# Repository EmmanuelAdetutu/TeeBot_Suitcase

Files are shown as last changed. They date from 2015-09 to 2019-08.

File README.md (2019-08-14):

# TeeBot_Suitcase!!
The folding Suitcase 3D printer.

Super thanks to all 42 Backers from Kickstarter for making this project possible. They all made it posible to share this project with everyone!!.

<b>***Teebot Specifications... Printed objects gallery</b> [Availaible here](http://3dstuffs.nl/teebot/)

<b>***Guide Photos of assembled sample</b> [Availaible here](https://www.flickr.com/photos/31259217@N06/albums/72157655761866343)

<b>***Youtube Video and print videos...</b>[Availaible here](https://www.youtube.com/watch?v=e_J-Re-Gbfc)

<b>***folow me on instagram...  </b>[#teebot3d](https://www.instagram.com/teebot3d/)

...always work in progress...

Comments, suggestion, contributions, errors,  info....what have you?
send me an email <b>info@3dstuffs.nl</b>

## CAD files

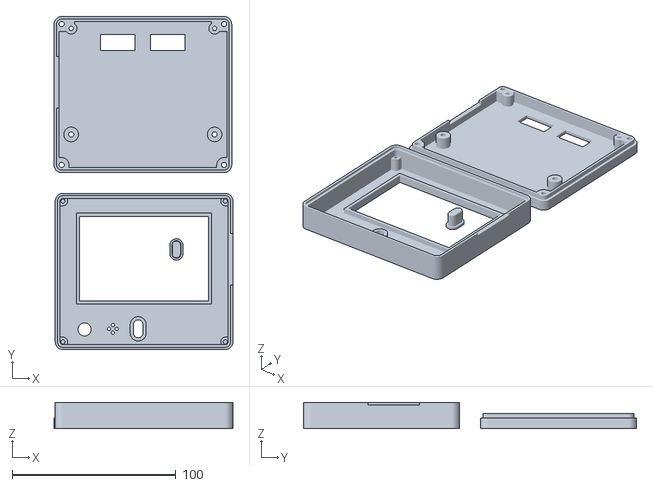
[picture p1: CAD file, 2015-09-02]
STL_Files/LCD_CASE_FULL_GRAPHIC.stl
109.3 x 203.5 x 16.1

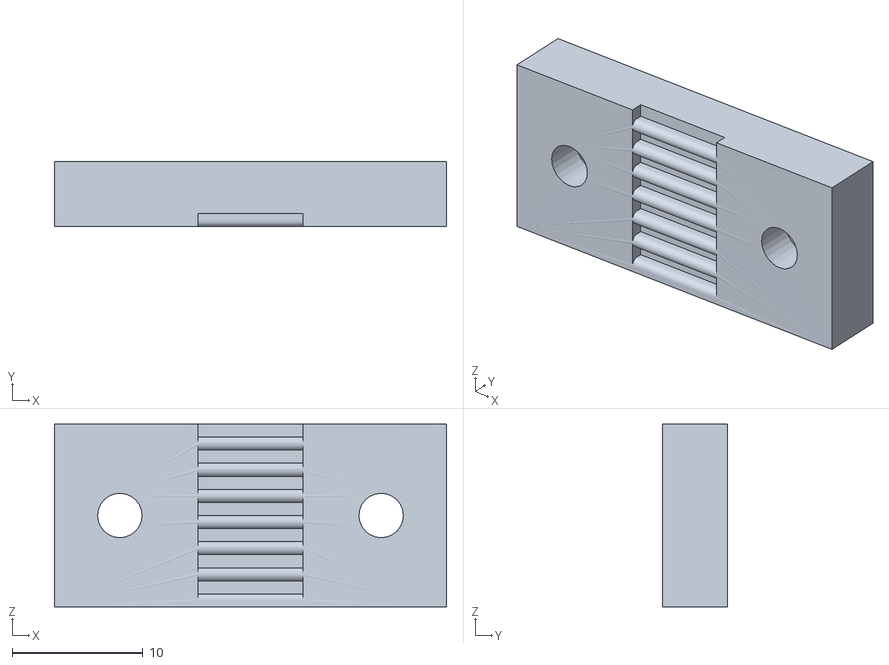
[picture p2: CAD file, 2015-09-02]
STL_Files/Y_Belt_Holder.stl
30.0 x 5.00 x 14.0

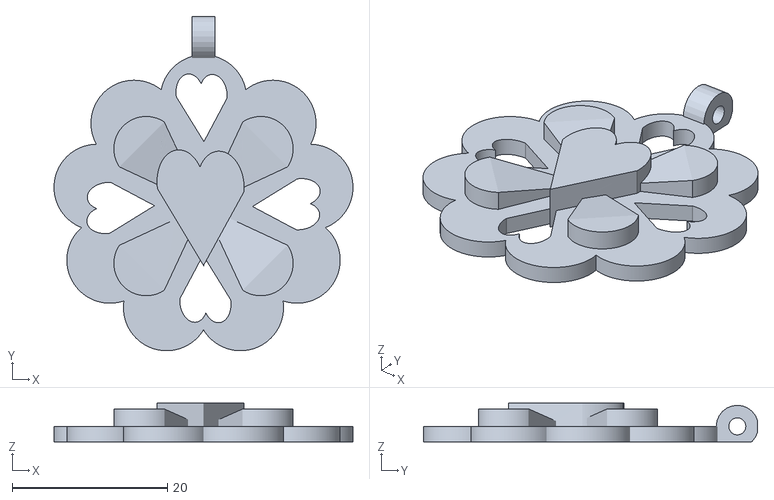
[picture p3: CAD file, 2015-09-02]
Test_STL_G_Code_Files/Test_Pendant.stl
38.6 x 43.1 x 5.00

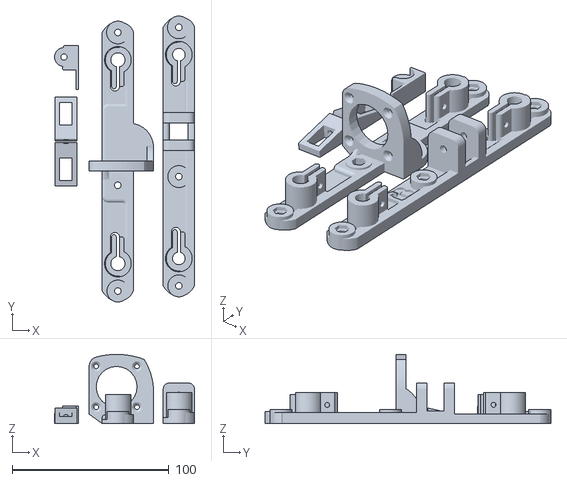
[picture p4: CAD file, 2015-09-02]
STL_Files/Y_Axis.stl
89.3 x 182.5 x 44.2

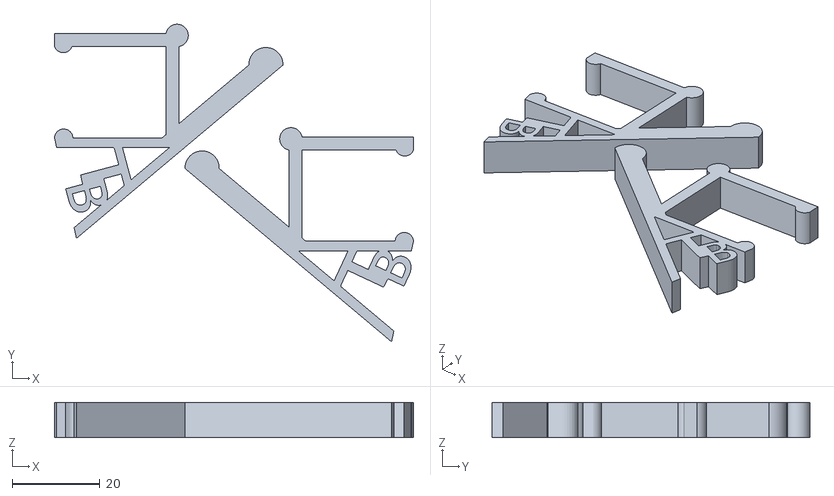
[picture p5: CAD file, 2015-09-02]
STL_Files/LCD_SUPPORT.stl
81.8 x 72.3 x 8.00

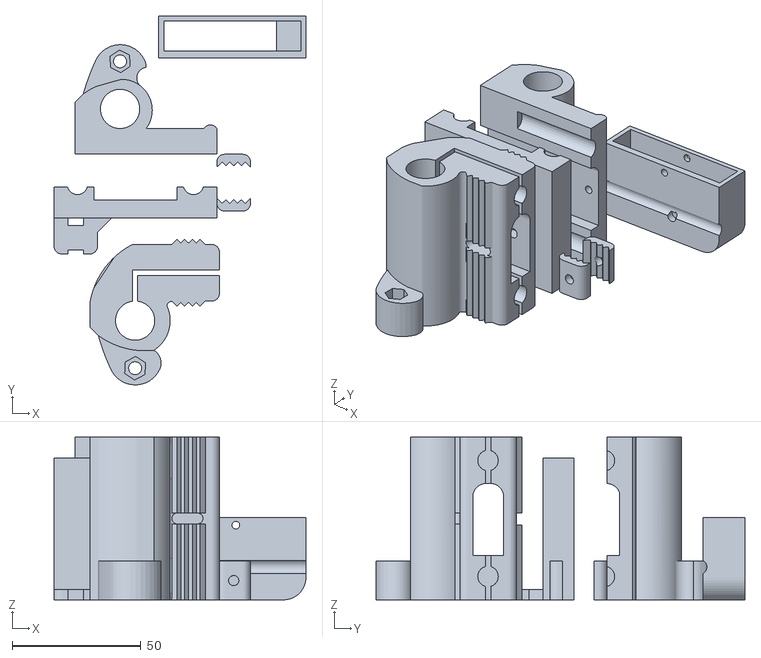
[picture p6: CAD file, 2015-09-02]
STL_Files/X_AXIS.stl
97.8 x 143.2 x 63.2

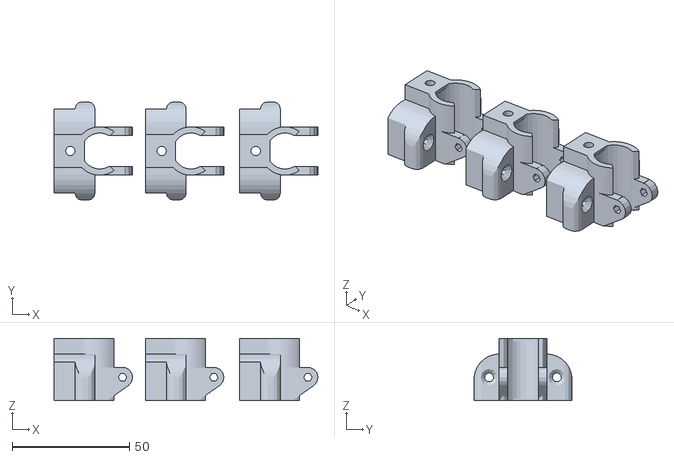
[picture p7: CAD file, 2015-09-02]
STL_Files/Y_Bearing.stl
112.8 x 42.0 x 26.7

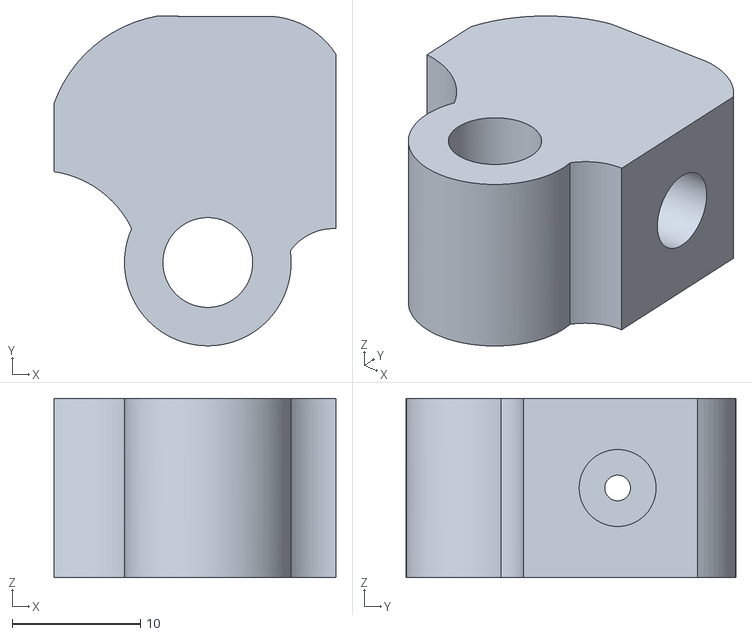
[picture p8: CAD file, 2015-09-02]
STL_Files/Spoolplug.stl
22.0 x 25.7 x 14.0

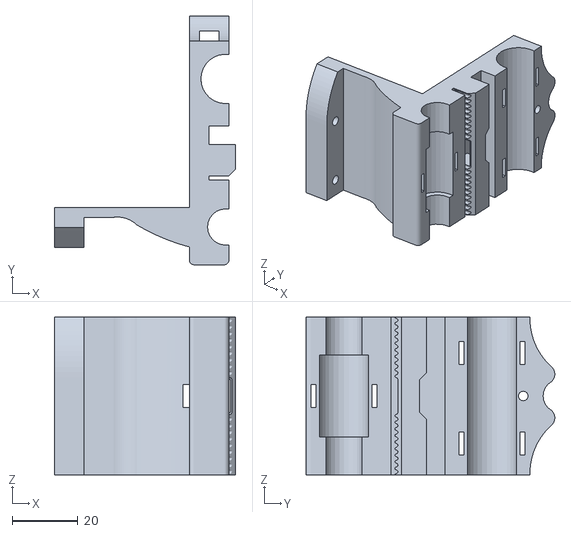
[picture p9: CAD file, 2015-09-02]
STL_Files/X_AXIS_CARRIAGE.stl
55.0 x 75.6 x 48.0

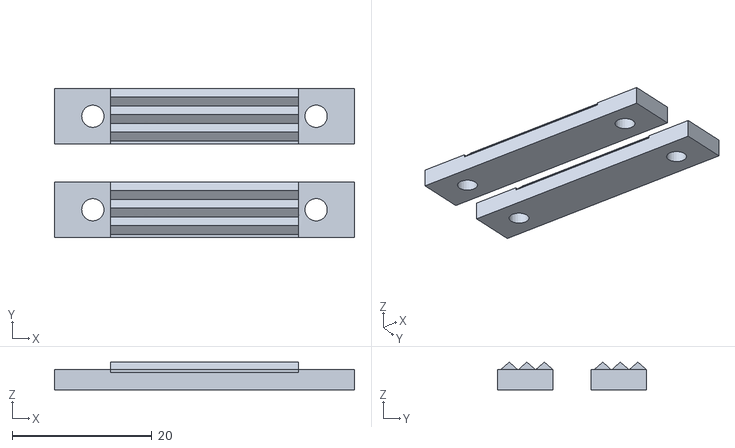
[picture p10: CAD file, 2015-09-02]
STL_Files/HARNESS_HOLDER.stl
43.0 x 21.4 x 4.00

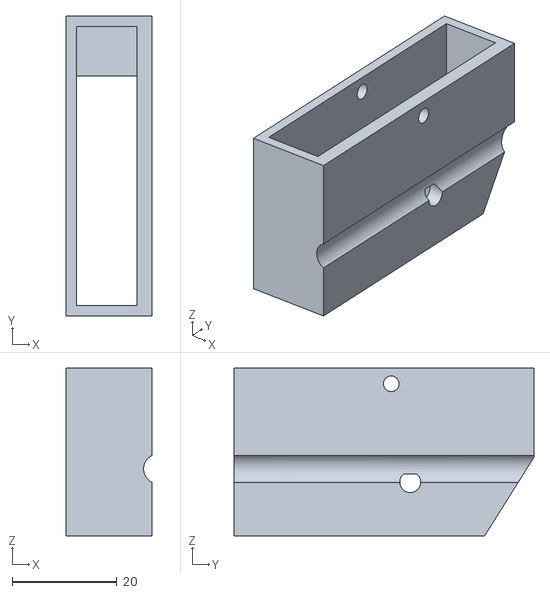
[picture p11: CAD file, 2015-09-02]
STL_Files/X_Lim_Stop.stl
16.4 x 57.2 x 32.0

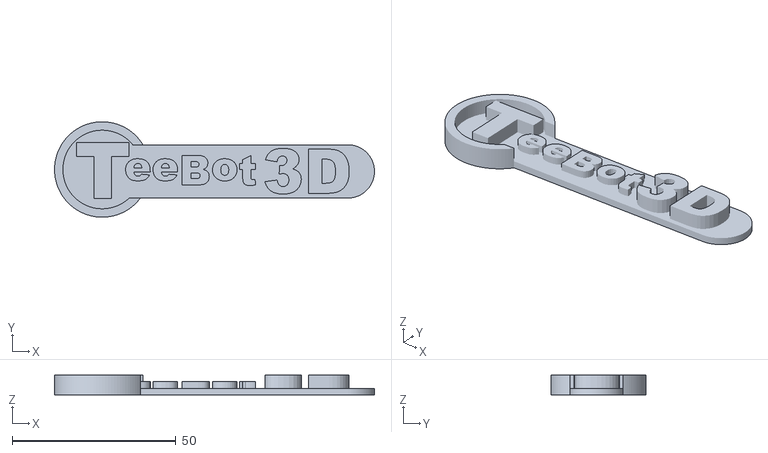
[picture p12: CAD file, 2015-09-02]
STL_Files/Teebot_Logo.stl
97.7 x 29.1 x 6.00

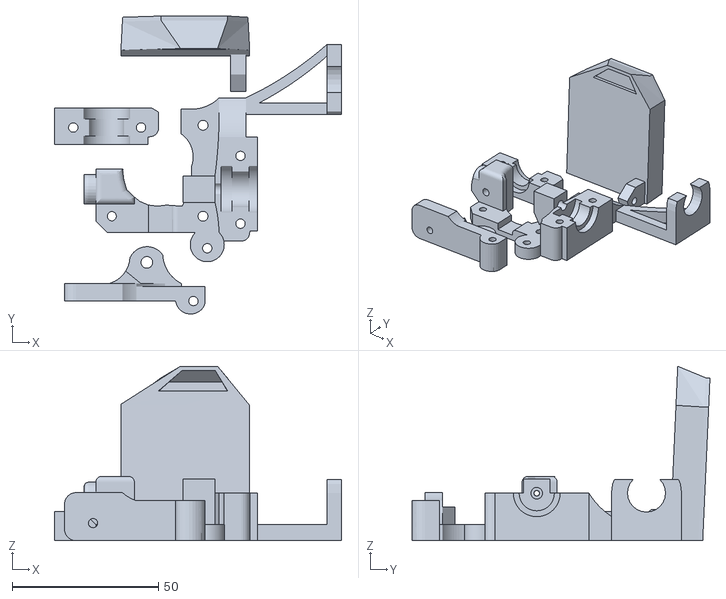
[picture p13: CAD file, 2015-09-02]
STL_Files/Teestruder_E3d_Lite.stl
98.2 x 101.8 x 59.6

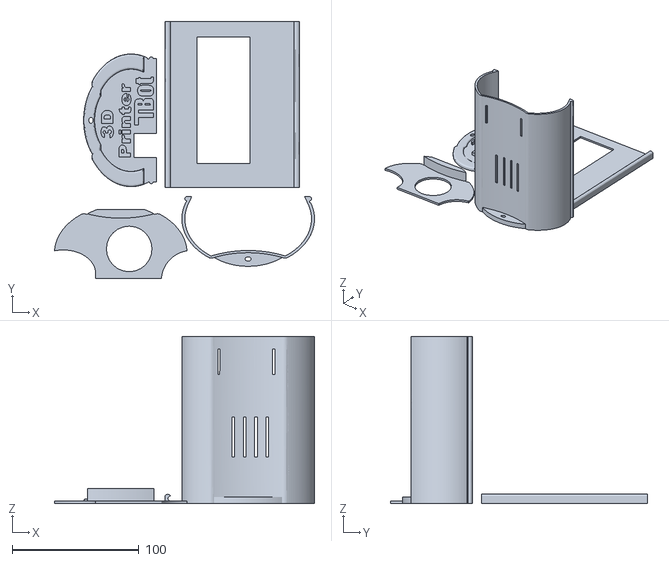
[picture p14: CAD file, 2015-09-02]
STL_Files/RAMPS_CASING.stl
205.3 x 203.0 x 131.9

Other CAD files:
STL_Files/Z_MOTOR_L_R.stl
STL_Files/Z_TOP_L_R.stl

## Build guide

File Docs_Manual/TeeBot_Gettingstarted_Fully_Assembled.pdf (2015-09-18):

# TeeBoT

The Opensource Suitcase 3D printer.

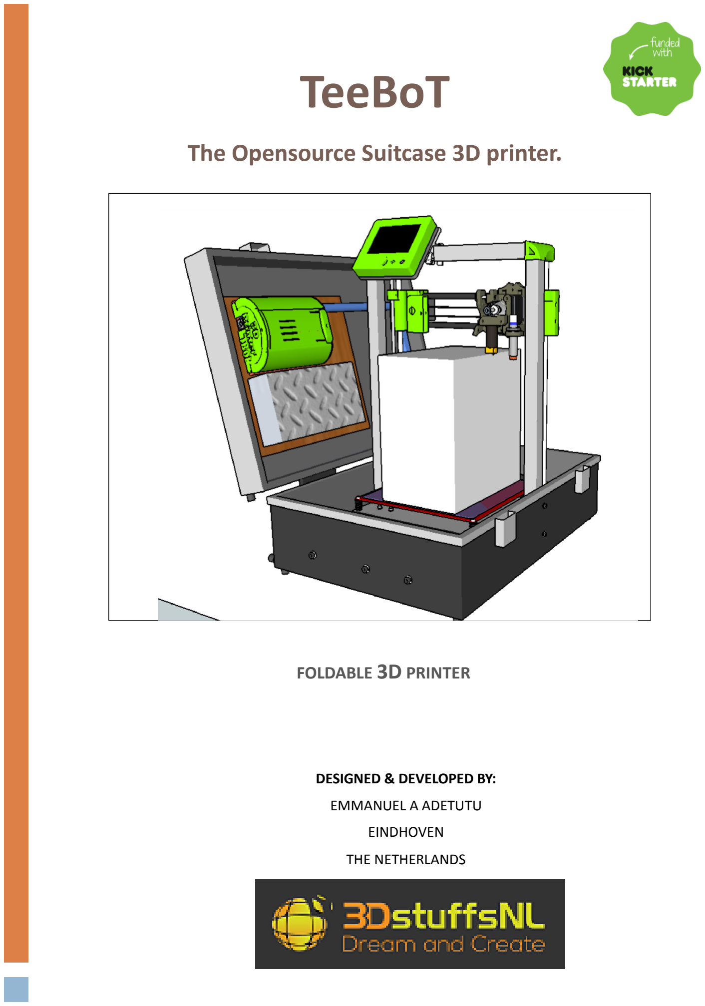
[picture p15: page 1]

DESIGNED & DEVELOPED BY:

EMMANUEL A ADETUTU

EINDHOVEN

THE NETHERLANDS

### FOLDABLE 3D PRINTER

### TABLE OF CONTENTS

INTRODUCTION.

Thanks for supporting TeeBot!! And welcome to the world of 3D printing if this is your first printer.

The TeeBot suitcase 3D printer was designed for 3D printing enthusiast on the move.

Terms and condition.

Please note you are completely responsible for the build, use, and operation of your 3D printer. Do not leave 3D printer unattended, always print in well ventilated places. Follow the safety guide for the filaments you use.

LIABILITY

# Neither 3DstuffsNL nor its designer or suppliers

shall be liable for any indirect, incidental,

# consequential, special, punitive, or exemplary damages which might arise out of the USE, BUILD

and OPERATION of your TeeBot 3D printers.

# CAUTION

A 3D printer works by melting plastic or materials at temperature up to 260 degrees or more!! Touching

the nozzle at that temperature will burn in less than a second!!

Do not touch a hot Nozzle or bed.

Do not leave a 3dprinter unattended!!,

Do not print in poorly ventilated rooms or space.

Printing any other material other than PLA requires extra ventilation.

You are responsible for any Item produce or the use of your Teebot 3D printer.

You cannot claim damages caused by the use of the Printer.

As with any tools, machine or equipment operating in a safe and clean environment with smoke alarms, fire extinguisher and most importantly absolute patience and care is required.

Keep children away from a working printer. (They tend to touch everything!!)

Starting from what is 3D printing? Going through the agonizing pain of building a DIY kit up to my first terrible print and now designing and building my own printers. I still have those moments where the prints fails… the filament runs out., un explainable out comes, print head crashing into beds, print fail after 98% (15 hour of print) and many many many many more…

…But the sight of a complete print and the translation of an imaginary object into real physical object within minutes keep me going.

A 3D printer is fun to work with. Enjoy and have fun 3D printing.

# GETTING STARTED WITH YOUR TEEBOT 3D

PRINTER.

This manual provides you with an overview on how to unpack and get started with you printer.

Please report any error detected in this documentation.

DAMAGE DURING TRANSPORT.

Care has been taken to ensure that the printer arrives undamaged. Please make a general inspection to ensure that you printer has not been damaged by the courier/shipping company.

If there are any broken unusable part please make a photo and send an email with the photo Taken.

UNBOXING THE PRINTER

1. Carefully remove all extra bags of Items included in supply.
2. Remove all bubble wrap round the printer by carefully cutting the tapes.
3. Carefully Open and Raise the printer cover

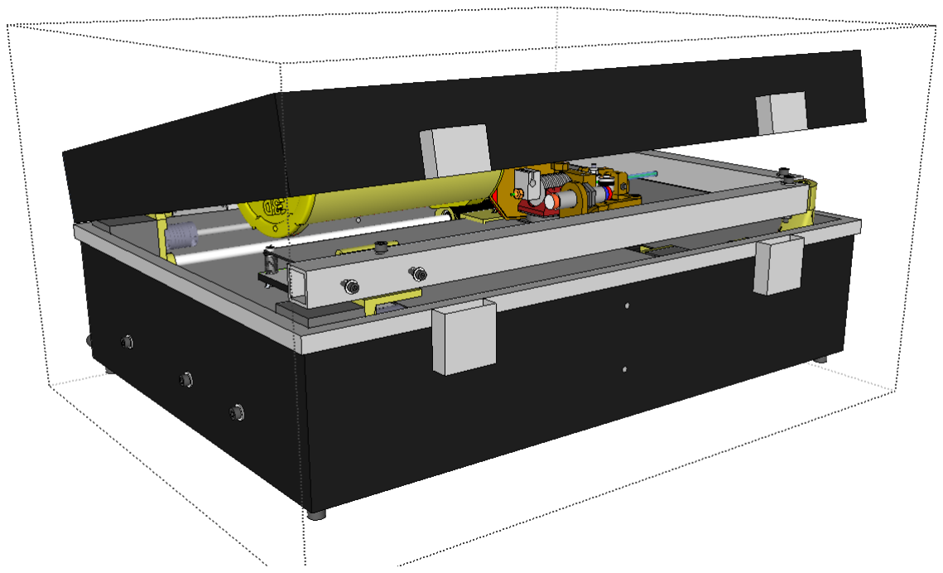
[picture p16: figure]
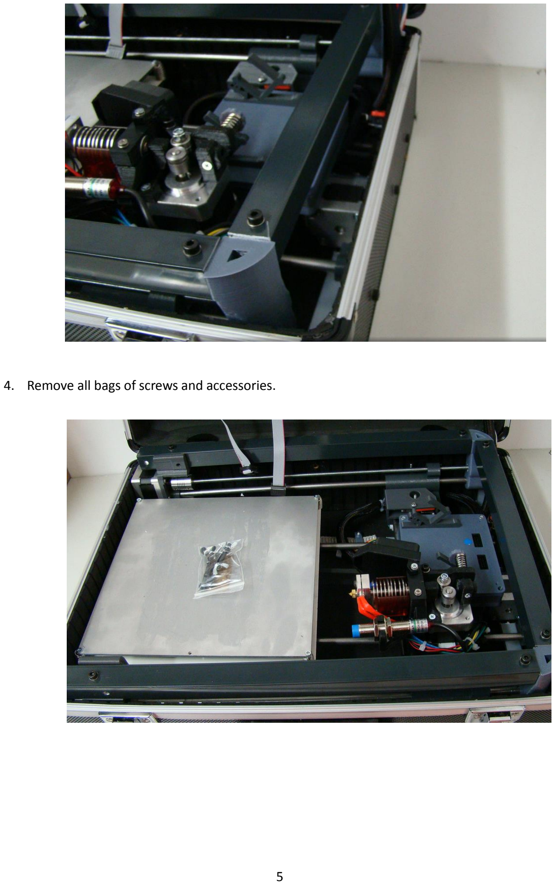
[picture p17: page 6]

4. Remove all bags of screws and accessories.

5. Raise the Z_axis/ print arm into position and use the four wing nuts to lock them down. Note

that the longer bolts is used in the top side.

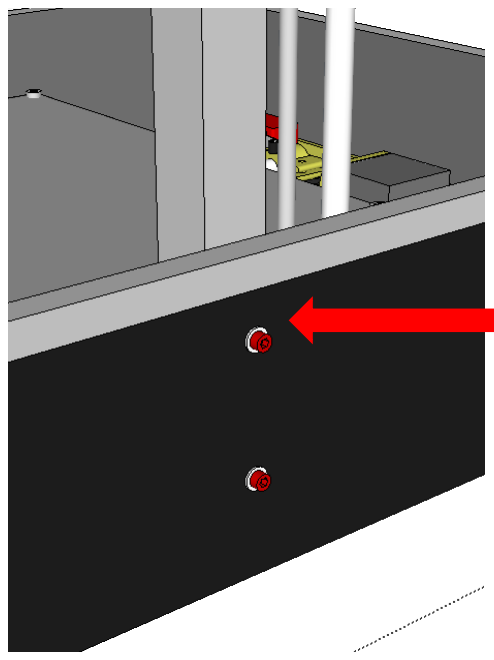
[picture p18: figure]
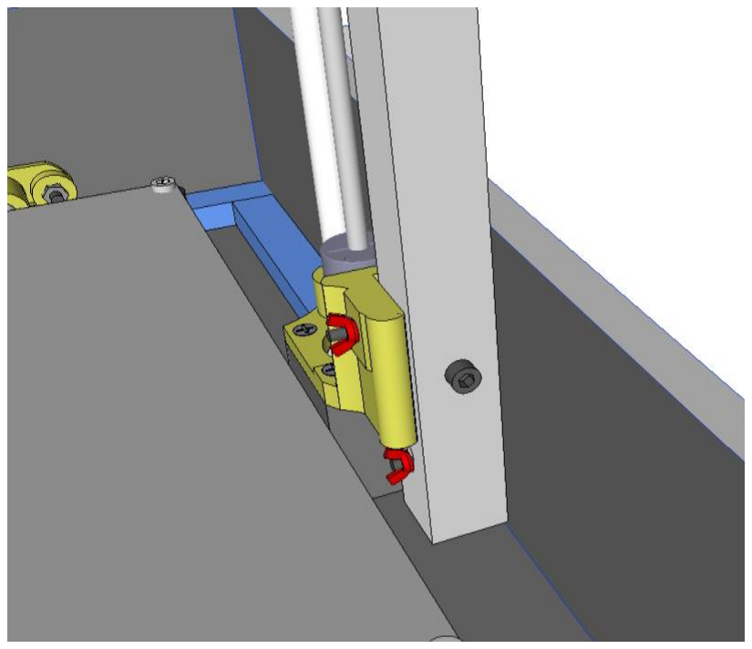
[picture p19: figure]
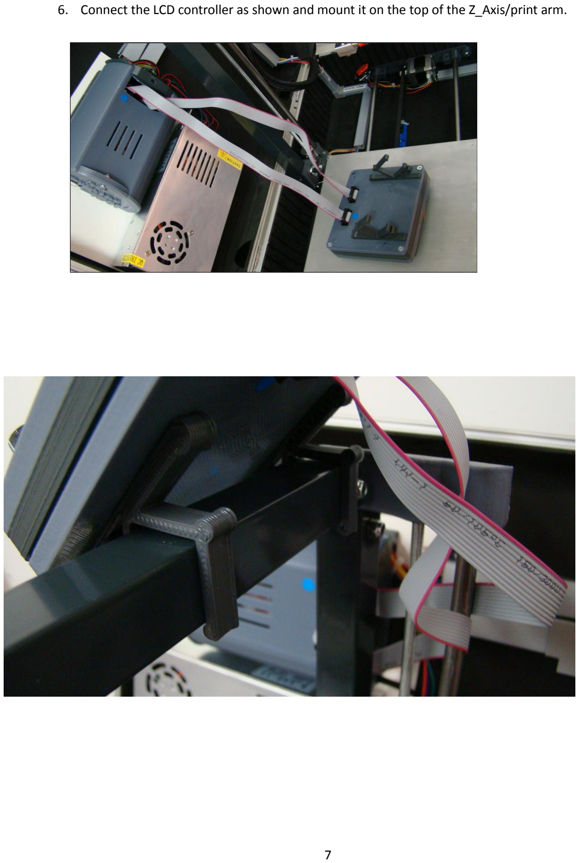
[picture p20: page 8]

6. Connect the LCD controller as shown and mount it on the top of the Z_Axis/print arm.

POWER CABLE AND ELECTRICITY VOLTAGE SETTING.

## Power setting:

Voltage Setting

Please check the voltage setting of the power supply, make sure it matches that of you mains electricity.

Default is set to EU 200-220V

Power plug

You will need to install a power cable to the power supply of your printer.

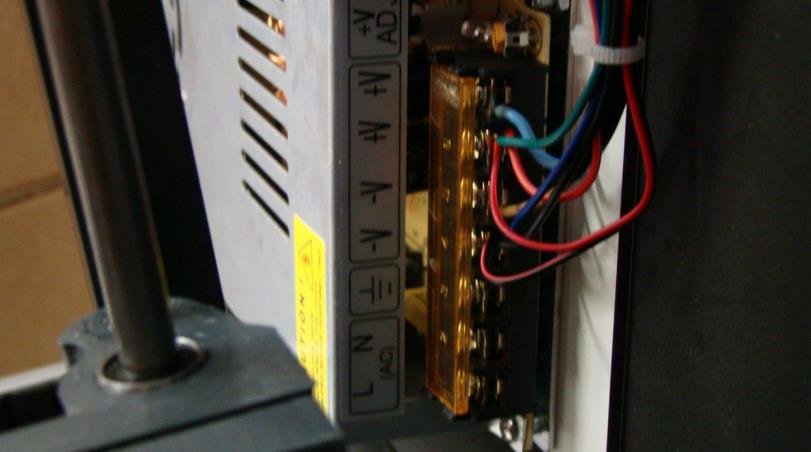
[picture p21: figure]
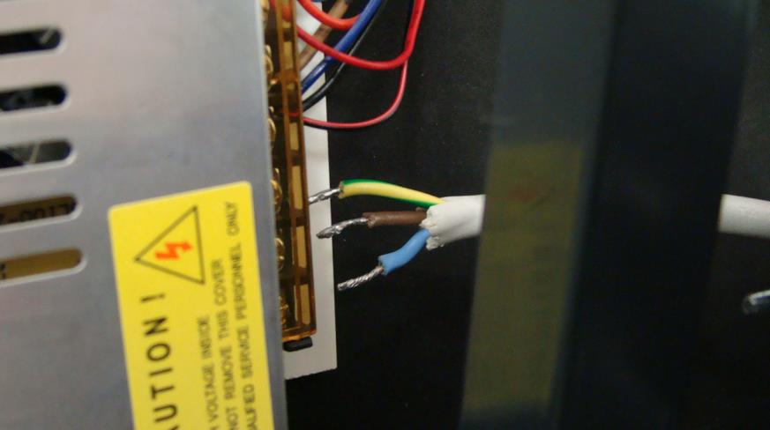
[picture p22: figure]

- Find a good power cable, any PC/ hot water Kettle cable is good enough.
- Cut the end, and strip the cables

### - Apply soldering to prevent the cable strands from loosening!

# FILAMENT SPOOL HOLDER

Due to packaging, the filament spool holder is not assembled, you will have to assemble the spool holder.

- Washers are on each side of the board.

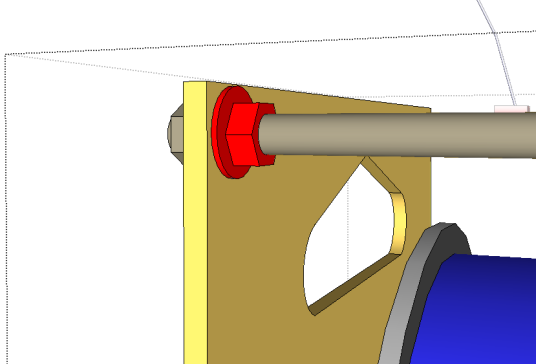
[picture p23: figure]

- The domed shape nuts are on the outside.
- The filament guide is in the middle of the top

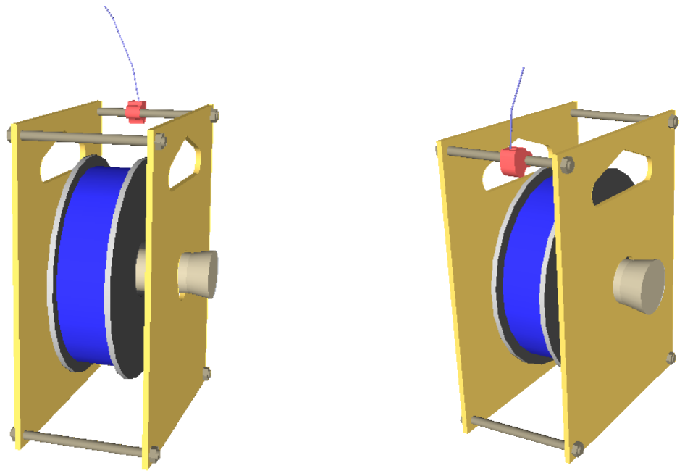
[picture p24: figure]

Make sure the hole on the small side is at least 2.5mm

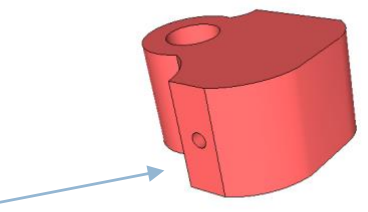
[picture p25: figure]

Make sure the hole on the big side can fit the supplied Teflon tube.

TEST PRINTING.

Your fully assembled printer has been tested, we leave a sample print object on the bed for you to see.

This object Gcode you can always print from the supplied SD card.

1. Start by ensuring that the Y axis Bed is able to touch and trigger the Y axis limit switch. Do this by moving the print Bed with your hands all the way to the back. If the limit switch has moved or not aligned please align it properly and ensure the switch can be triggered.

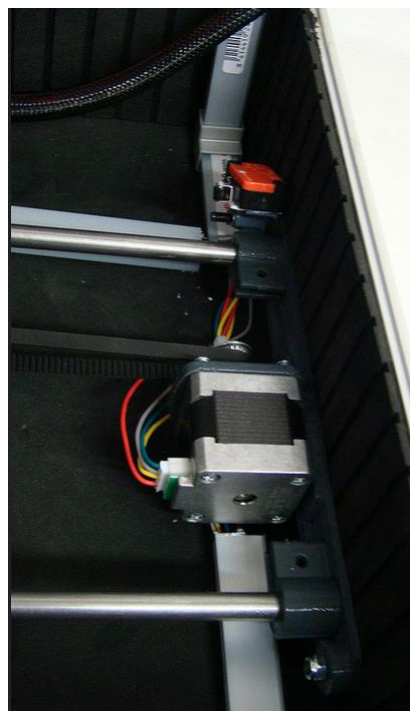
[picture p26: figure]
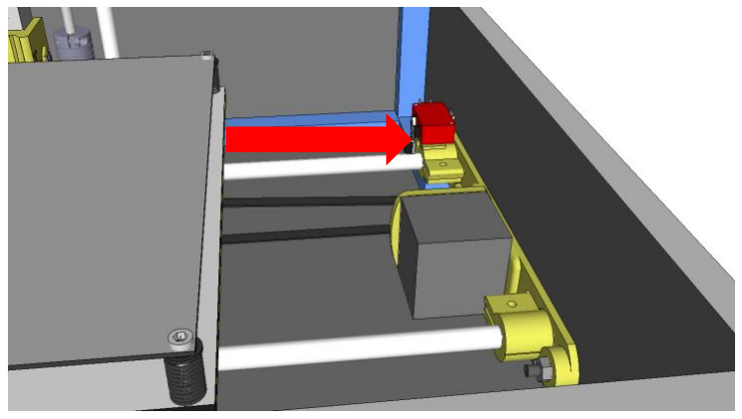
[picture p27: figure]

2. Do same for X Axis ensure that the extruder head when pushed all the way to the left is able to trigger the x Axis switch.

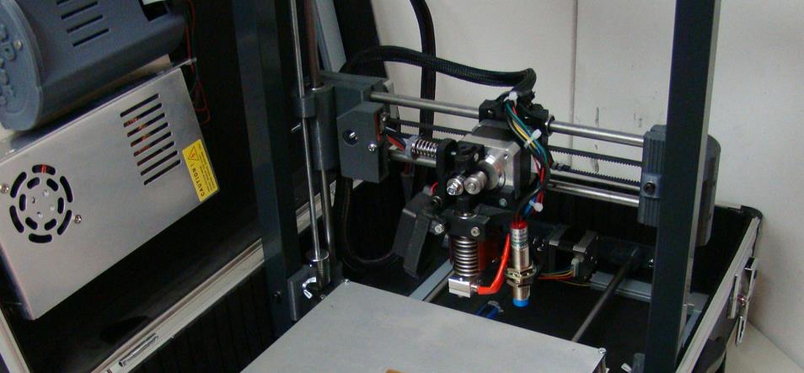
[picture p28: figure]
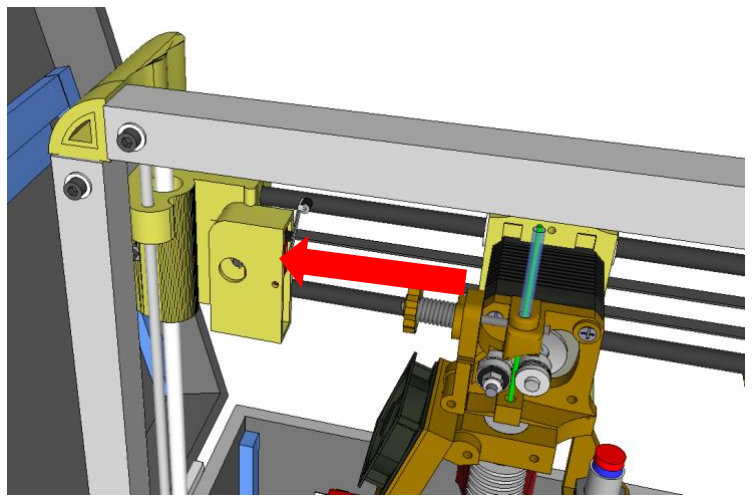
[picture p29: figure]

3. Ensure that the side cooling fan is tilted away from the hot end at an angle.

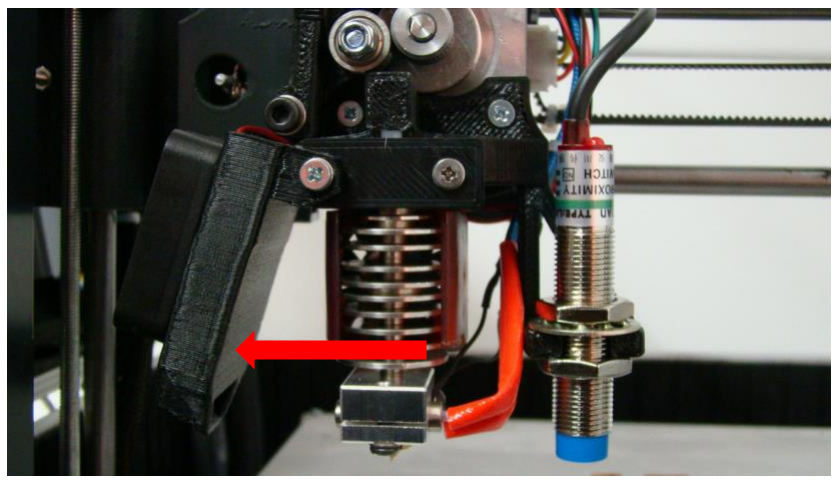
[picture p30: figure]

Correct positioning
of the side fan.

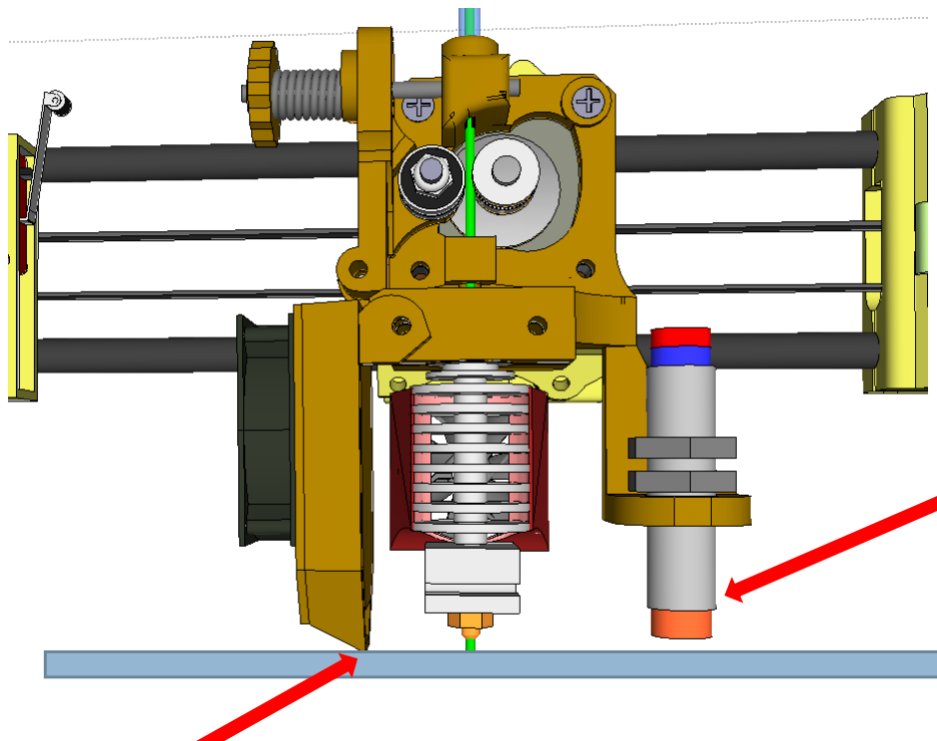
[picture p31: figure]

Wrong positioning of the side fan.

This will prevent the proximity sensor to move down enough to detect the heatbed when it is about to start printing.

If this happens you have to immediately turn of the printer and re align the printer.

Prevents the print head from going down.

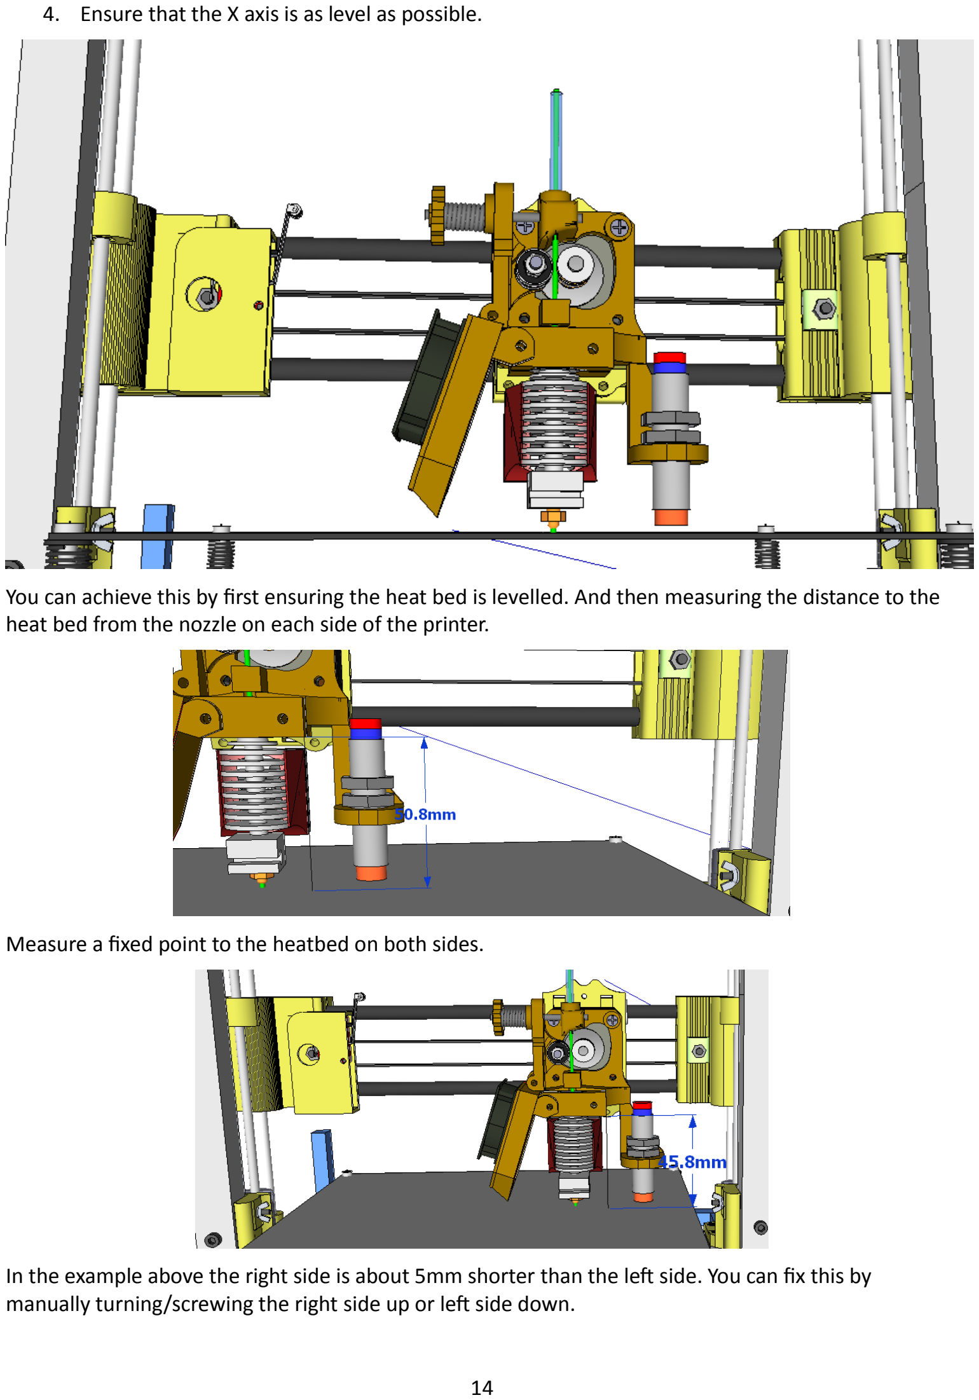
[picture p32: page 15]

4. Ensure that the X axis is as level as possible.

You can achieve this by first ensuring the heat bed is levelled. And then measuring the distance to the heat bed from the nozzle on each side of the printer.

Measure a fixed point to the heatbed on both sides.

In the example above the right side is about 5mm shorter than the left side. You can fix this by manually turning/screwing the right side up or left side down.

LEAKING NOZZLE

After a few use you might experience a leaking nozzle while printing. This can be fixed by tightening the hotend tip. While the hot end is hot, heated to around 180-200 degrees. Grab the block with a plier and use the correct size spanner tool to lock the nut as tight as possible.

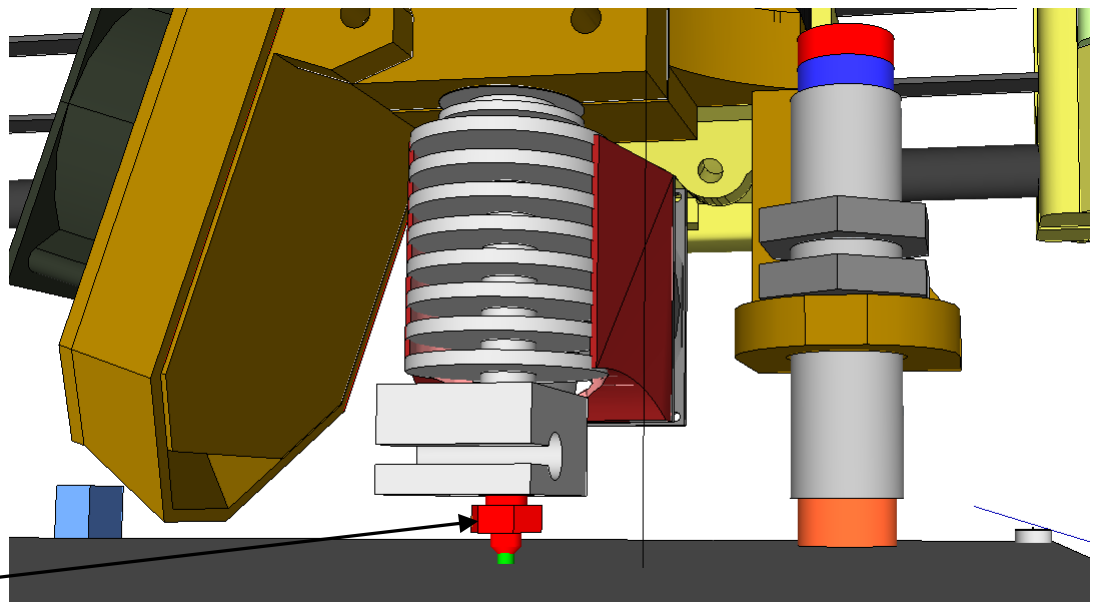
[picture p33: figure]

After tightening there should be at least 1 mm gap to the heat block!!

PRINTING CHECKLIST

1. Ensure that the gantry/upright column are fasten tight in place using the 4 wing nuts.
2. Ensure that nothing obstruct the X axis and you are able to manually (without power on the printer) push the X axis/Extruder head all the way left to the switch and to the extreme right.
3. Ensure that nothing obstruct the Y axis and you are able to manually (without power on the printer) push the X axis/Print bed all the way back to the switch and to the front as well.
4. Ensure that the X axis is leveled as described above, also that the side fan is in the right position.
5. Make sure the Printbed as a good layer of glue stick on it.
6. Snap away/Break or remove any leftover filament hanging at the tip of the nozzle. This can prevent the Z axis sensor from reaching the heatbed when cold and hard.

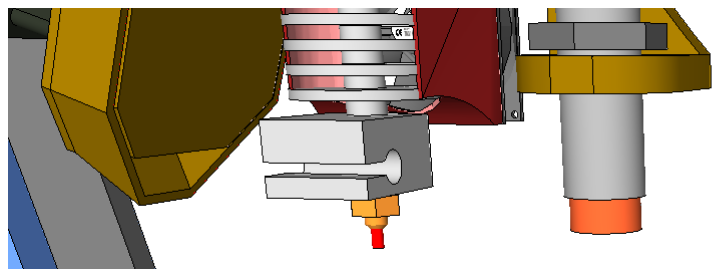
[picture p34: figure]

7. Load the prepared Gcode and start the print.
8. The first 4 layers are the most difficult, always be prepared to disconnect the printer in case anything goes wrong.

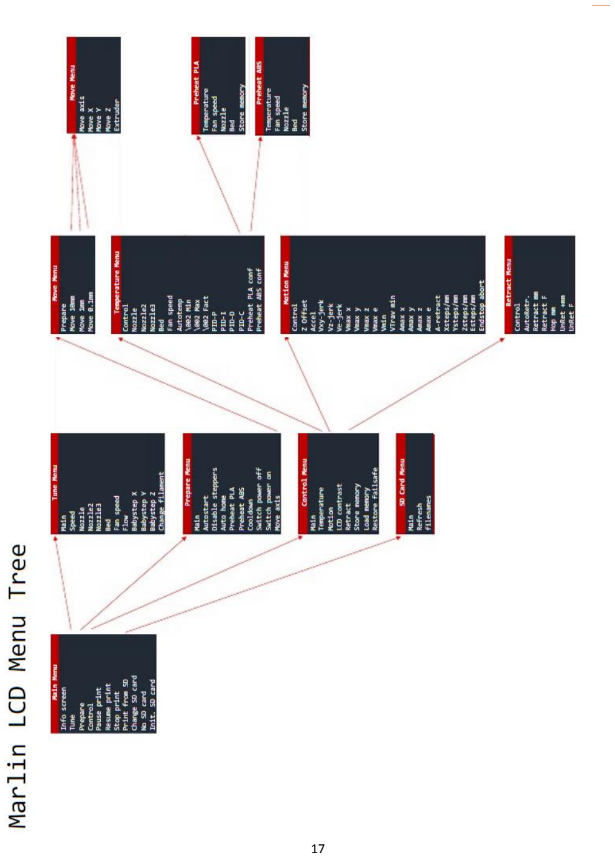
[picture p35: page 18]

SOME NICE MENUS

Print Speed adjusting: While printing, turning the knob from the main default page, Increases/decreases the print speed.
Change Filament Menu: [Tune – Change Filament]
- Pause the print,
- Move to a safe location
- Ejects the filaments and beeps until you insert a new filament.
- Continue printing by tapping on the knob.
Adjust fan speed: [Tune –Fan speed]

GENERAL 3D PRINTING PROCEDURE.

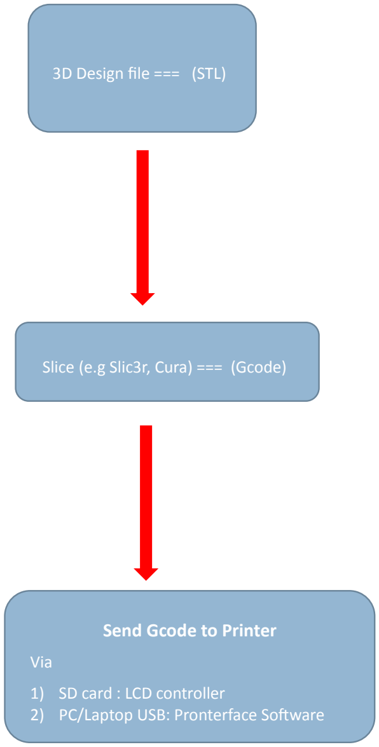
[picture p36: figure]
3D Design file === (STL); Slice (e.g Slic3r, Cura) === (Gcode); Send Gcode to Printer; Via; 1) SD card : LCD controller 2) PC/Laptop USB: Pronterface Software

GETTING HELP.

THE PRINTER IS A REPRAP STYLED 3D PRINTER.

1. Forums and blog online. I recommend searching online and reading about other people’s solution to similar problem via special forums/blog. E.g the Rerap forums (http://forums.reprap.org/)
2. Post photos of your questions or issues if possible make a short video and share. You are more likely to get an immediate answer.
3. Attend Makers meetup, hacker’s event and 3D printing events around you.
4. Send an email. info@3dstuffs.nl

# IMPORTANT CONTACTS

1. YouTube channel subscribe to the channel that way you don’t miss any new posted videos (https://www.youtube.com/user/teetopsy2)
2. Follow me on twitter for latest upgrades and realease. (https://twitter.com/teebotmax)
3. Online Photo Album on Flickr (https://www.flickr.com/photos/31259217@N06/albums/72157655761866343)
4. www.3Dstuffs.nl support the project by ordering directly from the designer/developer or any approved reseller/ Patners. You will also find STL files available for download.

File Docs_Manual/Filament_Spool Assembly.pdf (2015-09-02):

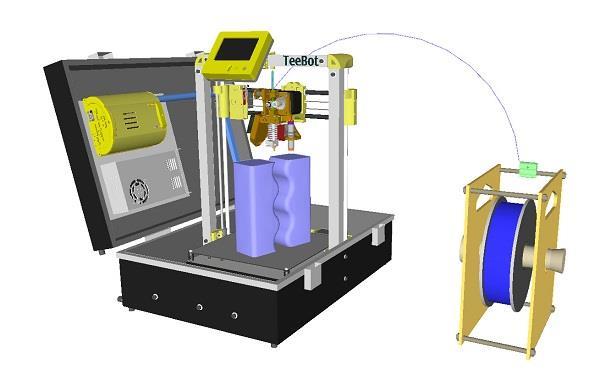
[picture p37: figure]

BY:

3DSTUFFSNL

EINDHOVEN

THE NETHERLANDS

# FILAMENT SPOOL HOLDER ASSEMBLY

Due to packaging, the filament spool holder is not assembled, you will have to assemble the spool holder.

- Washers are on each side of the board.


- The domed shape nuts are on the outside.
- The filament guide is in the middle of the top

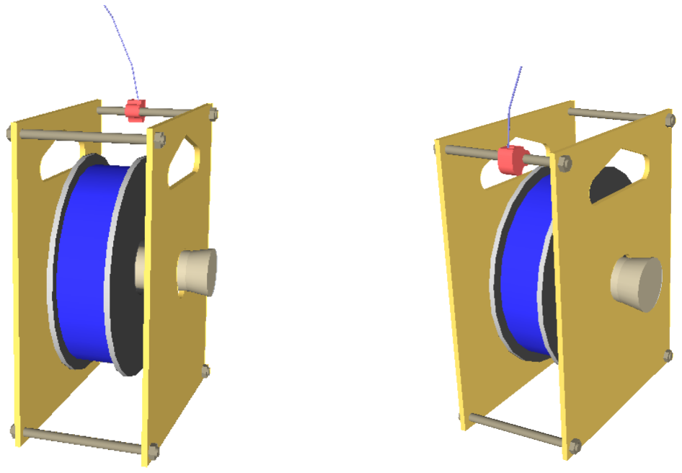
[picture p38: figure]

Make sure the hole on the small side is at least 2.5mm


Make sure the hole on the big side can fit the supplied Teflon tube.

## Ensure this by drilling out the small hole with a 2.5mm or

3mm drill bit and then the big hole with a 6mm drill bit.

The roller site between the hole in the board.

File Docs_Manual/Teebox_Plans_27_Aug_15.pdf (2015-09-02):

# TeeBox

The Suitcase 3D printer.

Eindhoven
The Netherlands

BY:

TeeBot Assembly Manual by 3DstuffsNL

5/15/2015 | TeeBot Suitcase | 1

### CONTENTS

INTRODUCTION.

Thanks for supporting TeeBot!! And welcome to the world of 3D printing if this is your first printer.

The TeeBot DIY kits, contains all key parts and components required for you to put together a working 3D printer. All parts have been carefully inspected and checked to ensure that you get a smooth build. For those who have successfully assembled a similar printer, assembling the TeeBot should be easy. Otherwise take the build as easy as possible.

Terms and condition.

Please note you are completely responsible for the build, use, and operation of your 3D printer. Do not leave 3D printer unattended, always print in well ventilated places. Follow the safety guide for the filaments you use.

# Liability

# Neither 3DstuffsNL nor its suppliers shall be liable

for any indirect, incidental, consequential, special,

# punitive, or exemplary damages which might arise out of the USE, BUILD and OPERATION of your

TeeBot printers.

Returns

Return is only possible on parts which have been damaged during shipping. If any part arrives broken or damaged please make a photo and send an email.

# WARNING

A 3D printer works by melting plastic or materials at temperature up to 200 degrees or more!! Touching

the nozzle at that temperature will burn in less than a second!!

Do not touch a hot Nozzle or bed.

Do not leave a 3dprinter unattended!!,

Do not print in poorly ventilated rooms or space.

Printing any other material other than PLA requires extra ventilation.

You are responsible for any Item produce or the use of the 3D printer.

You cannot claim damages caused by the use of the Printer.

As with any tools, machine or equipment operating in a safe and clean environment with smoke alarms,

fire extinguisher and most importantly absolute patience and care is required.

Keep children away from a working printer.

A 3D printer is fun to work with. Enjoy and have fun 3D printing.

# TRICKS AND TIP

It’s better to build your printer together with someone, much better if it’s built in a group where everyone can share their technical skills
All the skills required can be learnt, but it simply means prolonging the build time into weeks if not months. An easy way out is to embark on the adventure with someone who has the right tools and DIY mind.
The holes in the plastic might not match hundred percent of the time, its ok to drill out these holes with the right drill size while having the plastics in place.
Read the entire documentation to have an overview of the task ahead. Also to see where you might need help.
Again always follow all safety guidelines with using tools, machines and most importantly when working with electricity.

THE DESIGN.

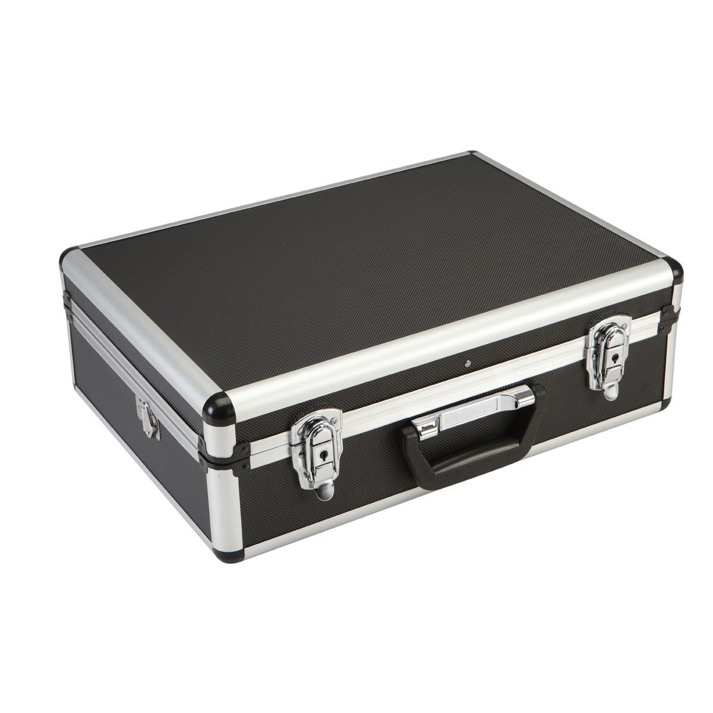
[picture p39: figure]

## “The journey of a thousand miles begins with a single step.”

TOOLS NEEDED.

Drill Bits : 4mm, 3mm, 8mm

Screw drivers, Pliers, Allen key set

# PART 1 ---Y AXIS (PRINT BED)

The rail on which the print platform rides is referred to as the Y axis. Upon completion of the Y axis you should have

- A free moving print platform.
- Installed stepper motor with adequate tension on belt drive
- Well secured rod/rail without play/movements.

Start by preparing the heatbed wire harness, then move on to tightening the belt and the Y axis end supports.

Fasten heatbed cable harness

Cable Harness

Fasten tight the heatbed cable harness onto the box, using

- 2) M3 X 20
- 2) M3 Washer
- 2) M3 lock nuts.

The line on which to fasten the cable is indicated on the wire harness.

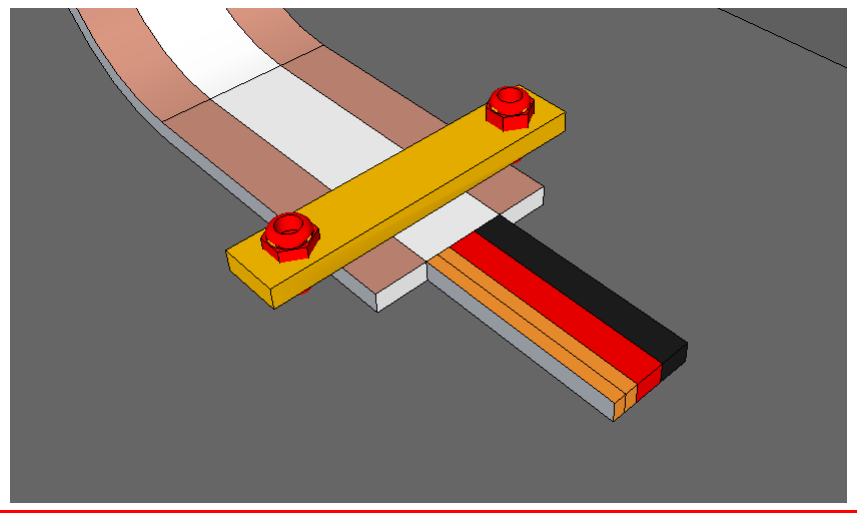
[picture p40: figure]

Prepare Y_AXIS motor

Y Axis Motor

Use

- 4) M3 x 10 bolts

to fasten the stepper motor into the Y_AXIS_MOTOR_END.

Note: The orientation of the stepper motor wire outlet is upwards!!

Install Y Idler bearing

Use

- 1) M4x 30 bolt
- 1) M4 Washer
- 1) M4 Nuts

fasten two idler bearing in place.

Note: The lock nut must sit properly in the Y_AXIS_IDLER. You might need to make the hole 4mm.

Prep Bearing Holder (x3)

Use

- 6) M3 Lock Nut

Insert 2 lock nuts each into the BEARING_HOLDER.

Note: For easy assembly, it is advisable to first drill out the holes with 3mm or 3.5mm drill.

If the nuts does not fit use a bolt by fastening it in.

Do this for all 3 Bearing holder.

Install bearing

Insert/press the LM8UU bearing into the holder by using one of the 8mm rod as a guide

Mount holder loosely on support board.

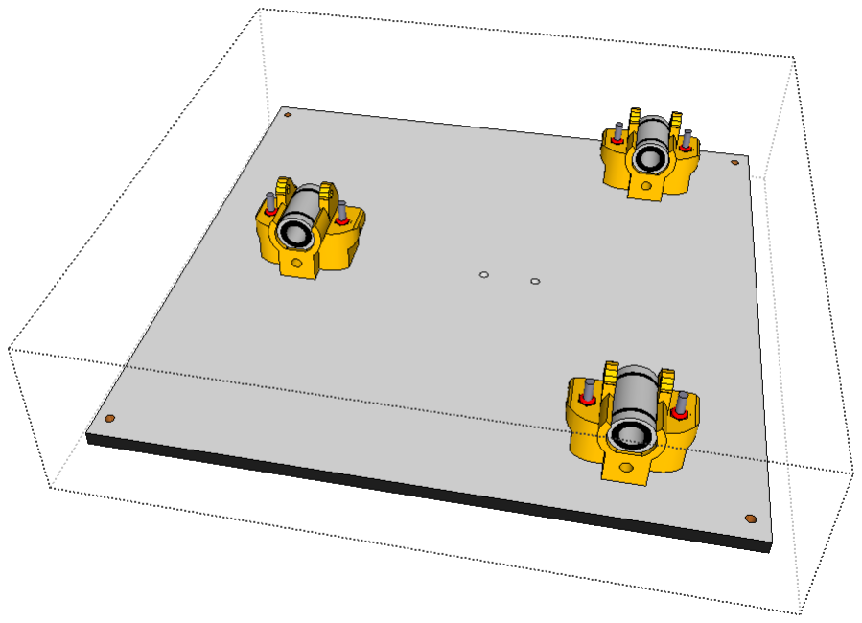
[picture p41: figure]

- 6) M3 X 30 Bolt

Using the M3 X 30mm mount all bearing holder on the board as shown.

Do not tighten fast yet!!

Insert the Y_AXIS_RODS

Tighten Belt

- 2) M3 X 20 Bolts
- 2) M3 Washer
- 2) M3 Lock Nuts

At Equal half fasten the belt to the board using 2 M3X20. These you can fasten tight

Mount Y_AXIS_MOTOR_END and Y_AXAIS_IDLER

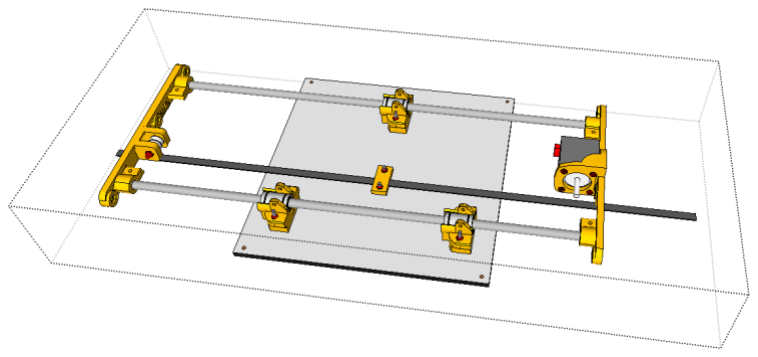
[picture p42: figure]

If the 8 MM rod does not slide in easily, use an 8mm drill in reverse direction to pass the hole. An alternative method is to blow some warm air/ hair dryer/ heat gun to soften the plastic a bit.

Note caution should be taken in inserting the rods.

Do not fasten the rods yet.

Mount Y_AXIS Into the 3D case

- 5) M4 X 20 Bolts
- 1) M4 X 30 Bolts
- 6) M4 Lock Nuts
- 6) M4 Washer

The longer M4 x 30 bolt is used on the motor side where the limit switch will sit.

Fasten tight. Washers are only on the outside of the box.

Note: The orientation of the assembly. The Y axis stepper is on the right hand side of the box

Mount Y_AXIS Into the 3D case

Mount Y_AXIS Into the 3D case

Tensioning the Y Axis belt

- 1) M3 x 30 Bolt
- 1) M3 x Lock nut

The belt is connected together and tensioned using the two belt connector.

Assemble the connector as shown.

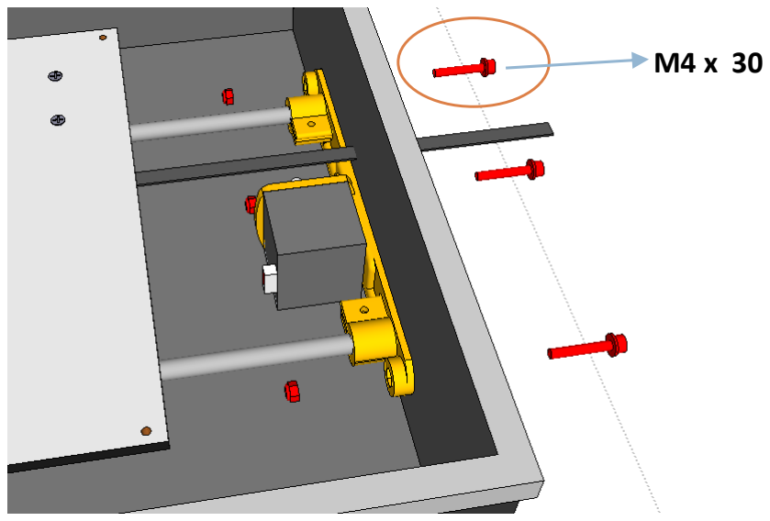
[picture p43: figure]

Assemble the connector as shown.

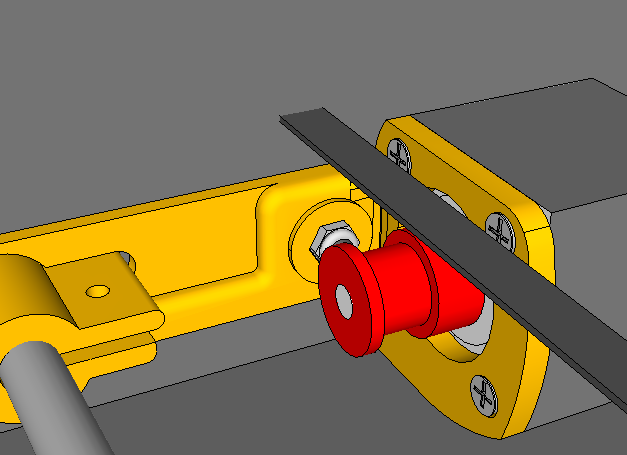
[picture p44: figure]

Slide one of the GT2 pulley in place. Do not fasten tight Yet.

Wrap the belt around pulley and idler sliding the print platform to the stepper motor side.

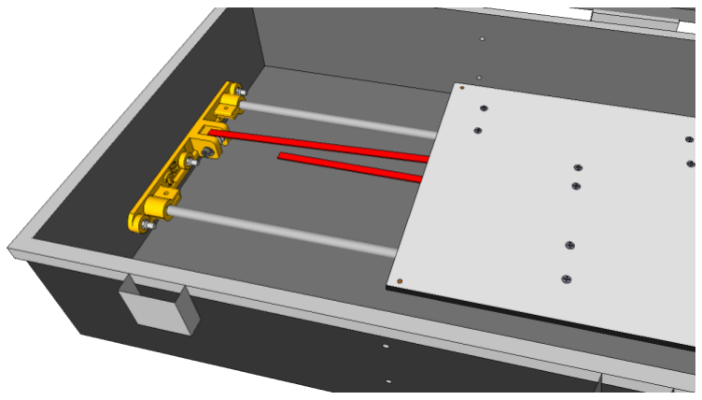
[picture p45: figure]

Wrap the belt around pulley and idler sliding the print platform to the stepper motor side.

Wrap the belt around tension assembly.

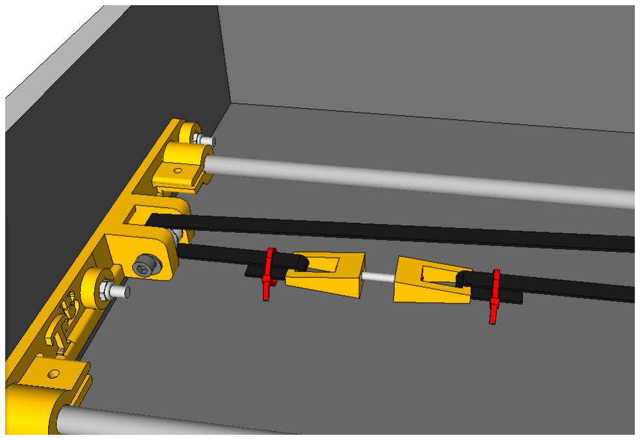
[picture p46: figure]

Secure the belt in place as tight as possible using the zip tie use two zip tie on each side.

Slide the print bed back and front to properly align the pulley and fasten tight the pulley.

At this point fasten tight all fasteners. Check each and every one of them to ensure none is forgotten.

If all goes well you have a completed Y_AXIS assembly. The print bed should slide easily on its rail with minimal effort.

The belt should be firm but not too much. Make sure the zip tie are well tensioned. If possible use two on each side of the belt.

# PART 2 ---Z AXIS (FRAME)

Assembling the Z axis.

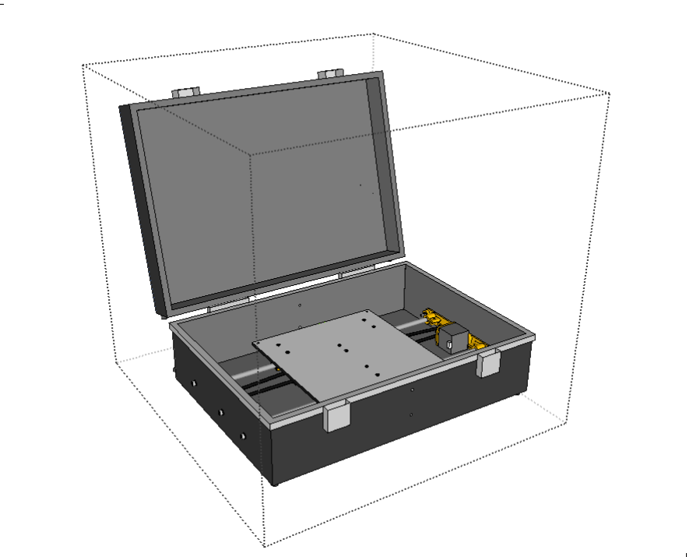
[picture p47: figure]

The Z Axis lifts the print nozzle(X Axis) up and down. The Z Axis is designed to be easily demountable for packing the 3d printer. It is held in place by 4 bolts and wing nuts for easy unpacking and assembling. Before printing and after long prints, it is advisable to check these for wing nuts to make sure they are properly fasten at all time.

The Z Axis is assembled by first mounting the poles on each sides and then installing the Z_threaded rods and smooth rods, the top section comes next and finally the X Axis.

Prepare the Z_Axis Motor.

Start by making sure the 8mm hole for the rod is free enough to take the 8mm rod. If not, in reverse motion use the drill with 8mm bit to clear and make the hole through. And file or make round the tip of the 8mm rods.

Mount two of the stepper motor

Next mount the stepper motors using the M3X 10mm screw.

Note: The orientation of the connector/cable front for the stepper motor

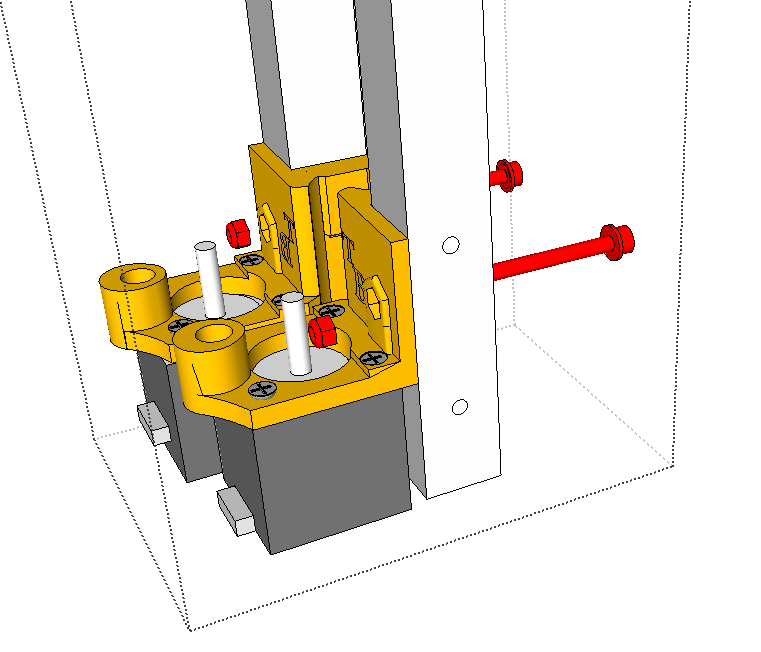
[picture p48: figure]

Next install the assembled motor on to each of the Z_POLE tubing.

Fasten Tight.

Use M4 x 30 bolts and nut with washers on the Aluminum side only.

Mount each Z-Pole into the box using

The longest mounting screw in the handle mount.

Use M4 x 50 for the top bolt and M4 x 40 for the bottom one.

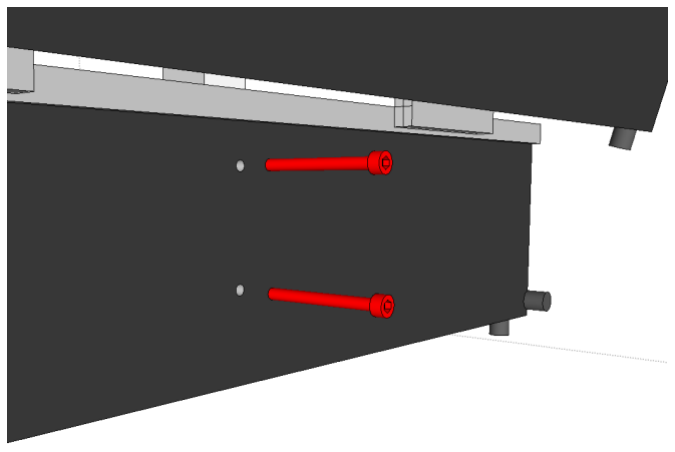
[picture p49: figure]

Mount each Z-Pole into the box using

The longest mounting screw in the handle mount.

Use M4 x 50 for the top bolt and M4 x 40 for the bottom one.

Insert the two Aluminum coupling into the Stepper motor.

Note: Do not fasten the lock nuts!!

Prepare the X_Axis Assemblies.

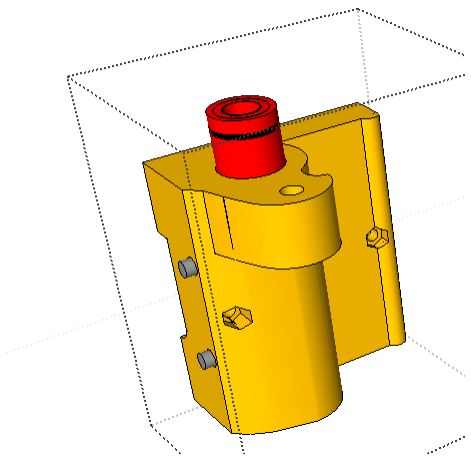
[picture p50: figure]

Insert two LM8UU linear bearing in each of the X_AXIS_ENDS

A little force is required in punching the bearing into the
X_AXIS_MOTOR end. Holding the plastic part in one hand while gently tapping it with a wood/ plastic/ rubber hammer does the trick.

Inserting the bearings in the X_AXIS_IDDLER ends is much easier.

Gently open the plastic and let the bearing slid all the way in.

Lock/ fasten all grub screw tight.

Mount the stepper motor on to the X_AXIS_MOTOR_BACK.

Before mounting the motor insert the long M3 x 40 bolts into the back side.

Mount the stepper motor on to the X_AXIS_MOTOR_BACK. Using the M3 x 10

Note the Direction of the Motor wiring / connector is downwards

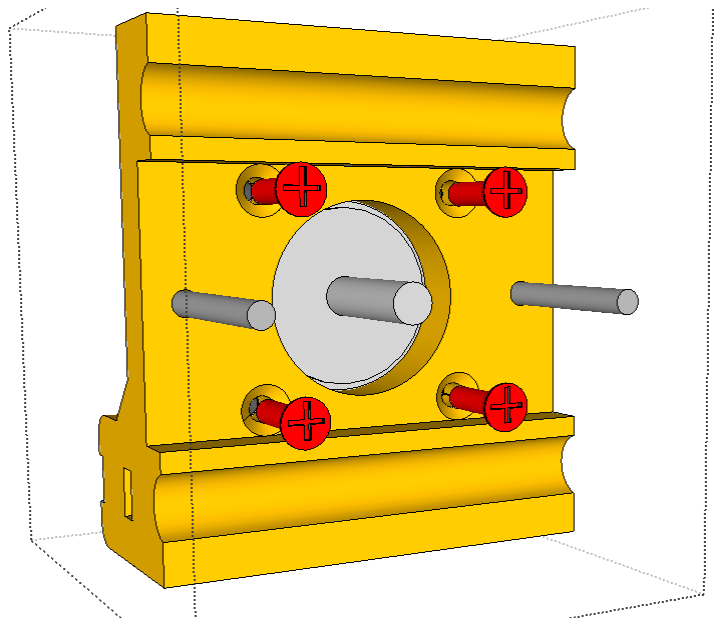
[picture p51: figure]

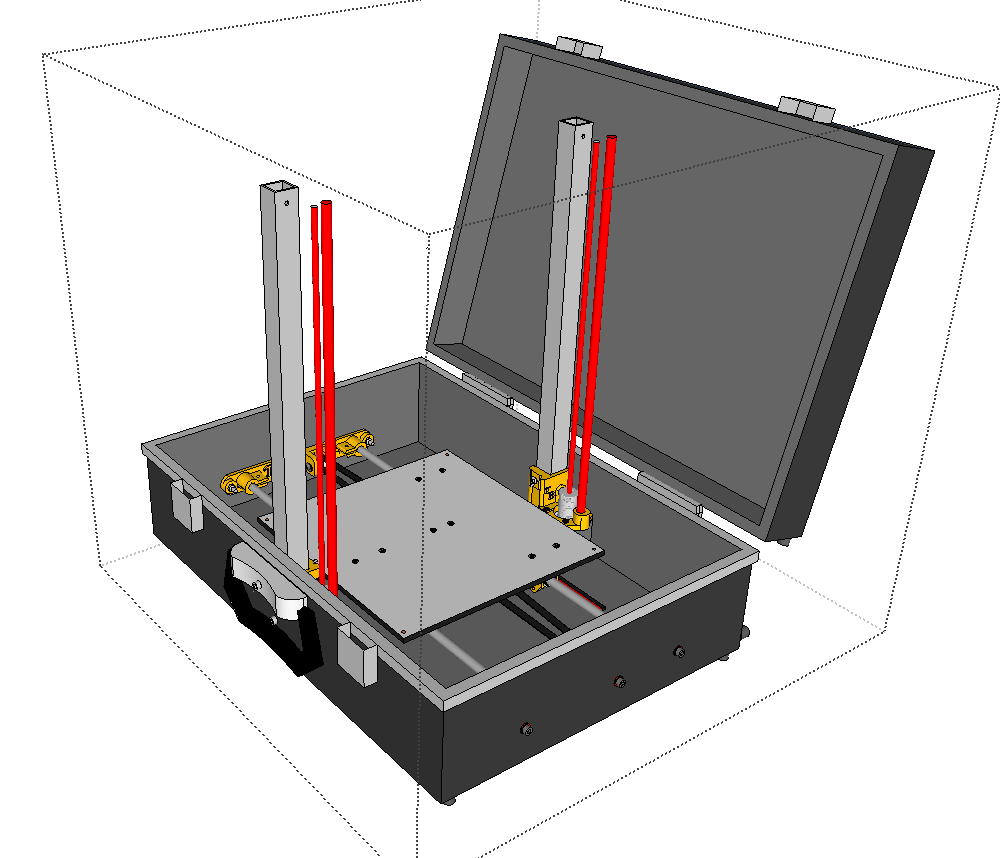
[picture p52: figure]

Insert the two M5 Threaded Rods, and the two M8 Smooth rods.

Use a plier to hold on the M8 and wiggle it left to right while gently pressing it into the hole in the plastic.

# PART 3 ---X AXIS

Slide in the prepared X_AXIS_IDLER and MOTOR end into the smooth rods, while rotating the threaded rods.

Slide in the X_AXIS_IDLER and
MOTOR end into the smooth rods, while twisting/screwing the threaded rods.

Try to thread each block down at least 4cm.

Next is to insert the X Axis rods. And screw it in place loosely

Note slide in two bearing for the top rod, and one for the lower rod.

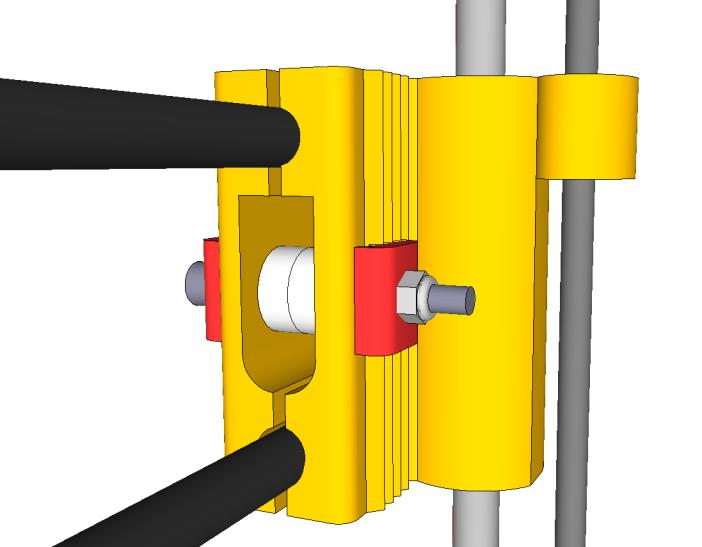
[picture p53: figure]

Insert the idler bearing and fasten loosely. Use M4 x 40.

Do not fasten the stepper motor assembly yet.

Insert the pulley and make sure it is align

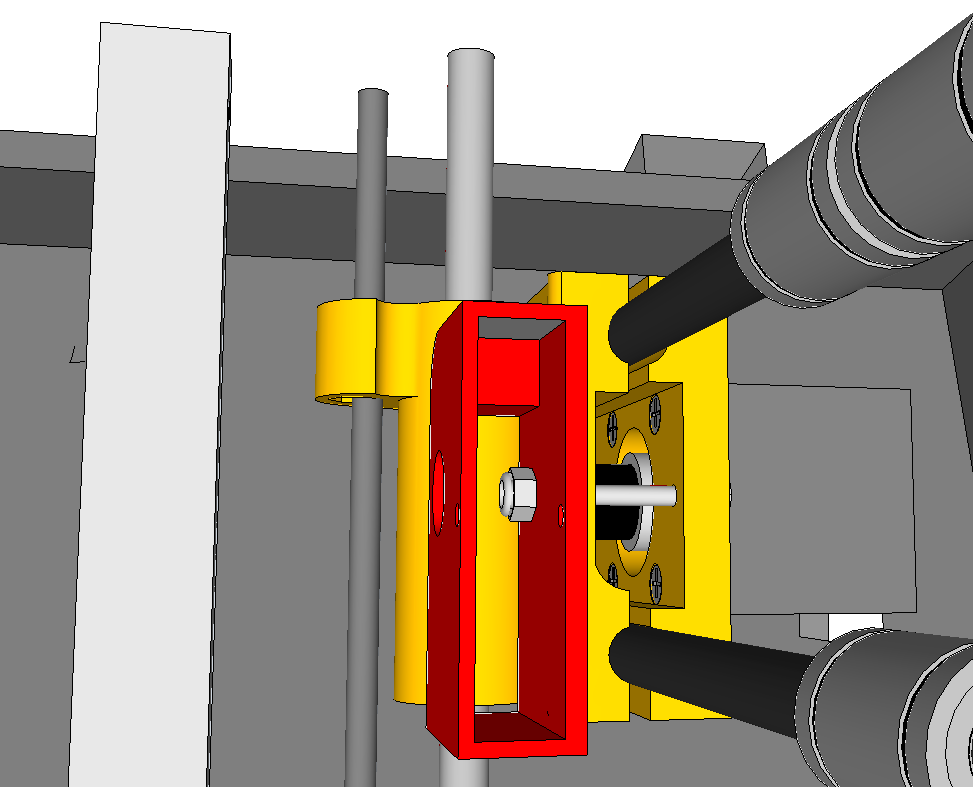
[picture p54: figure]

Mount the X_AXIS_LMIT_HOLDER and screw loosely in place.

Prepare the top frame assembly

Fasten tight the two M4 x 25 Bolt with washers on both sides.

Insert the Top frame assemble into the printer. Using a plier on each side the M8 rod should be wiggled into place.

Fasten tight all 4 corners use M4 x 25.

Fasten tight the X_AXIS_MOTOR on the 2 mounting M3 screws.

Also fasten the X_Motor_Iddler.

Prepare the X_Carriage Assembly.

Mount the X_axis_Carriage unto the bearing and fasten using zip ties.


Thread the belts into the machine.

There are different method to secure the belts in place.

First is looping each belt backwards.

Second is pulling it to the lower zip tie and locking it in place using another zip tie see image below.


With all frames fasten, pull the belt as tight as possible and lock in pace using the ziptie.

If need be the belt can
be further tighten by
slackening the idler and
moving it backwards.

Aluminum HeatBed installation


While tilting the Heatbed slightly.

- Solder on the power cables for the Heat bed.
- Tape the thermistor underneath the bed anywhere around the center is fine.
- Using 4 pcs of 30mm screw and 4 springs secure the heatbed in place with m3 lock nuts
- The height of the bed from the board does not matter I recommend 15 to 20mm.

At this point the assembly of the mechanical parts is complete, fasten in place all nuts and zip tie make sure both belts are as tensioned tight as possible.

Move all axis in all direction they should move freely with a slight stepping feeling of the stepper motors.

Try folding the 3D printer by loosening the 4 mounting bolt and lay the X axis down in the box it should close neatly.

Note when loose, the X axis belt tend to lose some of its tension this is fine. When mounted back in place it gains the tension back.


# PART 4 ---ELECTRONICS

Install the RAMPS ELECTRONICS.

The Ramps board supplied with the kit has been prepared and tested for use.

Use a Zip tie to fasten the Arduino board to the plastic parts.

Mount the board into the box using the four mount M3/20 bolts

Install in place the cable pipes.

As shown in the image. The cable pipes are labelled in the kit.

A =

B =

C =

D =

E =

F =

G =


Instal/instert the cooling fan it should snap into place with little effort.

Instal/instert the proximity sensor. The Proximity sensor has already been prepared to length the black cable is the Gnd /Negative connecting to the 12V power supply. The cable with a pin goes on the Zmin in the board while the third cable is the possitive connecting to the 12Vpower supply.


Using the Supplied Cables Make all connections as shown in the diagram above, Please Note D9 connects to the side extruder Fan. And the fan from the hotend is connected directly to the power supply/ always on.

Side Extruder Fan

Connection to the limit switch is using the alternating pins in the block as shown above, 2 pins are connected to the “ s” and “ –ve” for x and y axis. For Z axis using the Limit sensor only one pin is required and it is connected to the “ S” pin for Z axis. The reminder of the Z axis are connected to 5 volts + and ground. Note you will have to limit the voltage going to the sensor using two resistor. This has already been done in the DIY kit supply. Simply connect the S for the Z axis the other connections goes straight to the power supply.

# PART 9 (TESTING)

Before you start printing it is recommended that you test and confirm all connections are properly fitted. A wrong connection will most likely damage a part if not the whole board.

Testing and calibration is done via a PC, after all it set up you can resume to printing from the SD card.

NOTE!! When you need to make a new connection on the RAMPS board or double check existing connections, it is important to first disconnect the printer from the software then the USB cable and finally always unplug the power supply!! Any attempt to connect or disconnect from the Ramps board while still powered will ruin your board immediately!!

POWER SUPPLY

Download the latest Pronterface (http://koti.kapsi.fi/~kliment/printrun/) software from here (http://koti.kapsi.fi/~kliment/printrun/)

1. Make sure the power output from the power supply is 12V by measuring the voltage output with a multimeter. If you have the kit from 3DstuffsNL this is already done.
2. Connect only the Main power supply, Thermistor T1 ,T2, Heated Bed power and Hot end Power
3. Make connection to the printer via pronterface using a USB cable, and make sure the temperature reading is similar to that of the Room. (Note you ramps Board need to have been flashed/loaded with the correct version of Marlin firmware this is already don with the supplied Board)


4. The Heater and Bed display should be a temperature close the room temperature. If this tempertature is Zero double check all connections and try again.

HEAT BED AND HOTEND TESTING.

Testing the heat bed and Hotend can be done by raising their temperature.

- While connected to Pronterface set the heatbed and hotend Temperature to 70 degrees by typing it in the box and clicking set.
- You should see the temperature rise to 70 degrees after a few minutes. For the first time it is ok to smell some burnt plastic, oil. If the temperature fail to rise, double check the connection/ polarity of the heatbed, the hotend connection does not have polarity. You feel the temperature by touching the heat bed, be careful touching the hotend as the temperature might initially rise above 70 degree and then fall.

X AXIS AND LIMIT SWITCH TESTING

The next test is the X Axis, the aim here is to make sure that the X axis moves from left to right, and also that the limit switch is triggered when reached. Remember to always disconnect the USB cable and power supply first before making / changing any connection

- Connect the X axis motor and limit switch and connect the printer and power.
- Try to move the printer by 1 mm on the X axis. Do not attempt to move the printer by 100mm. This is done by using the move buttons on the software.


- Do this with a few clicks, +ve X is right direction, -ve X is left, if the printer move in opposite directions, fix this by flipping the X axis connector on the Ramps board. (Remember disconnect USB, and power supply first!!!).
- Place you hand on the X limit switch to activate the switch hold it down and try to move the x axis in the –ve direction it should not move. If it moves double check the connection and make sure you have the limit switch properly connected.

Y AXIS AND LIMIT SWITCH TESTING

The next test is the Y Axis, the aim here is to make sure that the Y axis moves from Front to Back, and also that the limit switch is triggered when reached. Remember to always disconnect the USB cable and power supply first before making / changing any connection.

Repeat the steps in X axis for the Y axis to make sure that the Y Axis limit is triggered and that the bed move in the right direction when moved +ve (forward away from the limit switch) –Ve backwards towards the limit switch.

Z AXIS AND LIMIT SWITCH TESTING

The Z axis is simple, bring a metal object close to the proximity sensor and the light should come on indicating that it is triggered. Check the direction of travel by ensuring –Ve goes upwards, and –Ve downwards.

EXTRUDER MOTOR TESTING

The extruder needs to rotate in the right direction while extruding. To be able to extrude, you will need to raise the temperature otherwise marlin will trigger cold extrusion and prevent the motor from moving.

- Set the heater temperature to 180
- Manually Insert a filament into the hotend going as far as possible, you should see it coming out from the nozzle
- Next extrude by 5mm, using the pronterface extrude button.
- Note the rotation of the extruder, it should be anticlockwise. If it rotates clockwise ejecting the filament from the hotend, you will have to flip the connection of the extruder motor.
Remember to always disconnect the USB cable and power supply first before making / changing any connection.

At this point you are safe to use the X and Y axis Home button to move the printer to the Home position by itself.

AUTO LEVEL TESTING

The DIY kit comes with preloaded marlin firmware which is enabled for Auto leveling. If you are sourcing the parts yourself a good video to watch in setting up auto leveling is Tom’s Guide (https://www.youtube.com/watch?v=EcGFLwj0pnA) on auto leveling. If you need the Modified marlin you can always send an email.

HOME ALL AXIS

After homing all axis the height of the extrusion nozzle should be just a little bit above the bed. ~ 1mm

At this point you are ready to 3D print. Note if you are sourcing your parts or using a different control board, all axis will need calibration to ensure that 1mm moved in the software actually translate to 1mm movement on the printer. This requires some little mathematics, updating of the firmware configuration settings and then flashing/ reloading of the firmware into the control board. There are many blogs, videos and topics online that covers calculating the correct steps for the stepper motor. Please follow this process for the board you are using.

3D PRINTING

Download the sample Gcode from our website if you do not have them, load it via pronterface and print.

If the printer prints too high in the air, the print will not stick to the bed, if the nozzle is in the heatbed scratching the aluminum heat bed it will not print also, you will hear a ticking sound from the extruder and notice a jerk of the filament. Please follow the step above on calibrating the auto Z level. Normally simply moving the proximity up or down by a few millimeter should do the trick.

After you are satisfy with the print, you can then move on to copy the same Gcode to an SD card and then 3d print from the SD card.

Do not try to rush your build!! When you are not sure it’s better to pause and find help online or simple send an email. It is much better to wait a day or two than waiting a week or two for a replacement parts and spending more.

SLIC3R SETTINGS

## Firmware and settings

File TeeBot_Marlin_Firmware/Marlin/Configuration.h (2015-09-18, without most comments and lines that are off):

#define CONFIGURATION_H
#define STRING_VERSION_CONFIG_H __DATE__ " " __TIME__ // build date and time
#define STRING_CONFIG_H_AUTHOR "(none, default config)" // Who made the changes.
#define SERIAL_PORT 0
#define BAUDRATE 250000
#define MOTHERBOARD 33
#define CUSTOM_MENDEL_NAME "TeeBot"
#define EXTRUDERS 1
#define POWER_SUPPLY 1
#define TEMP_SENSOR_0 5
#define TEMP_SENSOR_1 0
#define TEMP_SENSOR_2 0
#define TEMP_SENSOR_BED 5
#define MAX_REDUNDANT_TEMP_SENSOR_DIFF 10
#define TEMP_RESIDENCY_TIME 10  // (seconds)
#define TEMP_HYSTERESIS 3       // (degC) range of +/- temperatures considered "close" to the target one
#define TEMP_WINDOW     1       // (degC) Window around target to start the residency timer x degC early.
#define HEATER_0_MINTEMP 5
#define HEATER_1_MINTEMP 5
#define HEATER_2_MINTEMP 5
#define BED_MINTEMP 5
#define HEATER_0_MAXTEMP 260
#define HEATER_1_MAXTEMP 260
#define HEATER_2_MAXTEMP 260
#define BED_MAXTEMP 120
#define PIDTEMP
#define BANG_MAX 255 // limits current to nozzle while in bang-bang mode; 255=full current
#define PID_MAX 255 // limits current to nozzle while PID is active (see PID_FUNCTIONAL_RANGE below); 255=full current
  #define PID_FUNCTIONAL_RANGE 10 // If the temperature difference between the target temperature and the actual temperature
  #define PID_INTEGRAL_DRIVE_MAX 255  //limit for the integral term
  #define K1 0.95 //smoothing factor within the PID
  #define PID_dT ((16.0 * 8.0)/(F_CPU / 64.0 / 256.0)) //sampling period of the temperature routine
    #define  DEFAULT_Kp 22.2
    #define  DEFAULT_Ki 1.08
    #define  DEFAULT_Kd 114
#define MAX_BED_POWER 255 // limits duty cycle to bed; 255=full current
#define PREVENT_DANGEROUS_EXTRUDE
#define PREVENT_LENGTHY_EXTRUDE
#define EXTRUDE_MINTEMP 170
#define EXTRUDE_MAXLENGTH (X_MAX_LENGTH+Y_MAX_LENGTH) //prevent extrusion of very large distances.
#define ENDSTOPPULLUPS // Comment this out (using // at the start of the line) to disable the endstop pullup resistors
  #define ENDSTOPPULLUP_XMAX
  #define ENDSTOPPULLUP_YMAX
  #define ENDSTOPPULLUP_ZMAX
  #define ENDSTOPPULLUP_XMIN
  #define ENDSTOPPULLUP_YMIN
const bool X_MIN_ENDSTOP_INVERTING = false; // set to true to invert the logic of the endstop.
const bool Y_MIN_ENDSTOP_INVERTING = false; // set to true to invert the logic of the endstop.
const bool Z_MIN_ENDSTOP_INVERTING = true; // set to true to invert the logic of the endstop.
const bool X_MAX_ENDSTOP_INVERTING = true; // set to true to invert the logic of the endstop.
const bool Y_MAX_ENDSTOP_INVERTING = true; // set to true to invert the logic of the endstop.
const bool Z_MAX_ENDSTOP_INVERTING = true; // set to true to invert the logic of the endstop.
#if defined(COREXY) && !defined(DISABLE_MAX_ENDSTOPS)
  #define DISABLE_MAX_ENDSTOPS
#endif
#define X_ENABLE_ON 0
#define Y_ENABLE_ON 0
#define Z_ENABLE_ON 0
#define E_ENABLE_ON 0 // For all extruders
#define DISABLE_X false
#define DISABLE_Y false
#define DISABLE_Z false
#define DISABLE_E false // For all extruders
#define INVERT_X_DIR false    // for Mendel set to false, for Orca set to true
#define INVERT_Y_DIR false    // for Mendel set to true, for Orca set to false
#define INVERT_Z_DIR false     // for Mendel set to false, for Orca set to true
#define INVERT_E0_DIR false   // for direct drive extruder v9 set to true, for geared extruder set to false
#define INVERT_E1_DIR false    // for direct drive extruder v9 set to true, for geared extruder set to false
#define INVERT_E2_DIR false   // for direct drive extruder v9 set to true, for geared extruder set to false
#define X_HOME_DIR -1
#define Y_HOME_DIR -1
#define Z_HOME_DIR -1
#define min_software_endstops true // If true, axis won't move to coordinates less than HOME_POS.
#define max_software_endstops true  // If true, axis won't move to coordinates greater than the defined lengths below.
#define X_MAX_POS 120
#define X_MIN_POS 0
#define Y_MAX_POS 200
#define Y_MIN_POS 0
#define Z_MAX_POS 190
#define Z_MIN_POS 0
#define X_MAX_LENGTH (X_MAX_POS - X_MIN_POS)
#define Y_MAX_LENGTH (Y_MAX_POS - Y_MIN_POS)
#define Z_MAX_LENGTH (Z_MAX_POS - Z_MIN_POS)
#define ENABLE_AUTO_BED_LEVELING // Delete the comment to enable (remove // at the start of the line)
  #define LEFT_PROBE_BED_POSITION 45
  #define RIGHT_PROBE_BED_POSITION 120
  #define BACK_PROBE_BED_POSITION 170
  #define FRONT_PROBE_BED_POSITION 20
  #define X_PROBE_OFFSET_FROM_EXTRUDER 40
  #define Y_PROBE_OFFSET_FROM_EXTRUDER 0
  #define Z_PROBE_OFFSET_FROM_EXTRUDER -0.4
  #define Z_RAISE_BEFORE_HOMING 2       // (in mm) Raise Z before homing (G28) for Probe Clearance.
  #define XY_TRAVEL_SPEED 8000         // X and Y axis travel speed between probes, in mm/min
  #define Z_RAISE_BEFORE_PROBING 2    //How much the extruder will be raised before traveling to the first probing point.
  #define Z_RAISE_BETWEEN_PROBINGS 2  //How much the extruder will be raised when traveling from between next probing points
  #define Z_SAFE_HOMING   // This feature is meant to avoid Z homing with probe outside the bed area.
    #define Z_SAFE_HOMING_X_POINT (X_MAX_LENGTH/2)    // X point for Z homing when homing all axis (G28)
    #define Z_SAFE_HOMING_Y_POINT (Y_MAX_LENGTH/2)    // Y point for Z homing when homing all axis (G28)
  #define ACCURATE_BED_LEVELING
    #define ACCURATE_BED_LEVELING_POINTS 2
#define MANUAL_X_HOME_POS 0
#define MANUAL_Y_HOME_POS 0
#define MANUAL_Z_HOME_POS 0
#define NUM_AXIS 4 // The axis order in all axis related arrays is X, Y, Z, E
#define HOMING_FEEDRATE {1500, 1500, 120, 0}  // set the homing speeds (mm/min)
#define DEFAULT_AXIS_STEPS_PER_UNIT   {100,100,4002.769,87.49}  // default steps per
#define DEFAULT_MAX_FEEDRATE          {400, 400, 2, 45}    // (mm/sec)
#define DEFAULT_MAX_ACCELERATION      {4000,4000,50,4000}    // X, Y, Z, E maximum start speed for accelerated moves. E default values are good for skeinforge 40+, for older versions raise them a lot.
#define DEFAULT_ACCELERATION          800    // X, Y, Z and E max acceleration in mm/s^2 for printing moves
#define DEFAULT_RETRACT_ACCELERATION  1000   // X, Y, Z and E max acceleration in mm/s^2 for retracts
#define DEFAULT_XYJERK                15.0    // (mm/sec)
#define DEFAULT_ZJERK                 0.3     // (mm/sec)
#define DEFAULT_EJERK                 5.0    // (mm/sec)
#define EEPROM_SETTINGS
#define EEPROM_CHITCHAT
#define PLA_PREHEAT_HOTEND_TEMP 180
#define PLA_PREHEAT_HPB_TEMP 70
#define PLA_PREHEAT_FAN_SPEED 255   // Insert Value between 0 and 255
#define ABS_PREHEAT_HOTEND_TEMP 240
#define ABS_PREHEAT_HPB_TEMP 100
#define ABS_PREHEAT_FAN_SPEED 255   // Insert Value between 0 and 255
#define ULTIPANEL  //the ultipanel as on thingiverse
#define REPRAP_DISCOUNT_FULL_GRAPHIC_SMART_CONTROLLER
 #define DOGLCD
 #define U8GLIB_ST7920
 #define REPRAP_DISCOUNT_SMART_CONTROLLER
 #define ULTIPANEL
 #define NEWPANEL
  #define NEWPANEL  //enable this if you have a click-encoder panel
  #define SDSUPPORT
  #define ULTRA_LCD
    #define LCD_WIDTH 20
    #define LCD_HEIGHT 4
#  define DEFAULT_LCD_CONTRAST 32
#define SOFT_PWM_SCALE 0
#include "Configuration_adv.h"
#include "thermistortables.h"

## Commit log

2015-09-02 TeeBot SuitCase
    [HARNESS_HOLDER.stl, LCD_CASE_FULL_GRAPHIC.stl, LCD_SUPPORT.stl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]
2015-09-18 Added Marlin Firmware
    Added Marlin Firmware, Getting started PDF and organize the docs into
    single folder.
    [Configuration.h, Configuration_adv.h, Menu Plans.xlsx]
